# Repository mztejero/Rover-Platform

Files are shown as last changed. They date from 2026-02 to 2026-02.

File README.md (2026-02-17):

# Rover-Platform
ESP-IDF firmware, KiCad PCB, and Fusion360 Cad files  for a Rovere Platform

<p align="center">
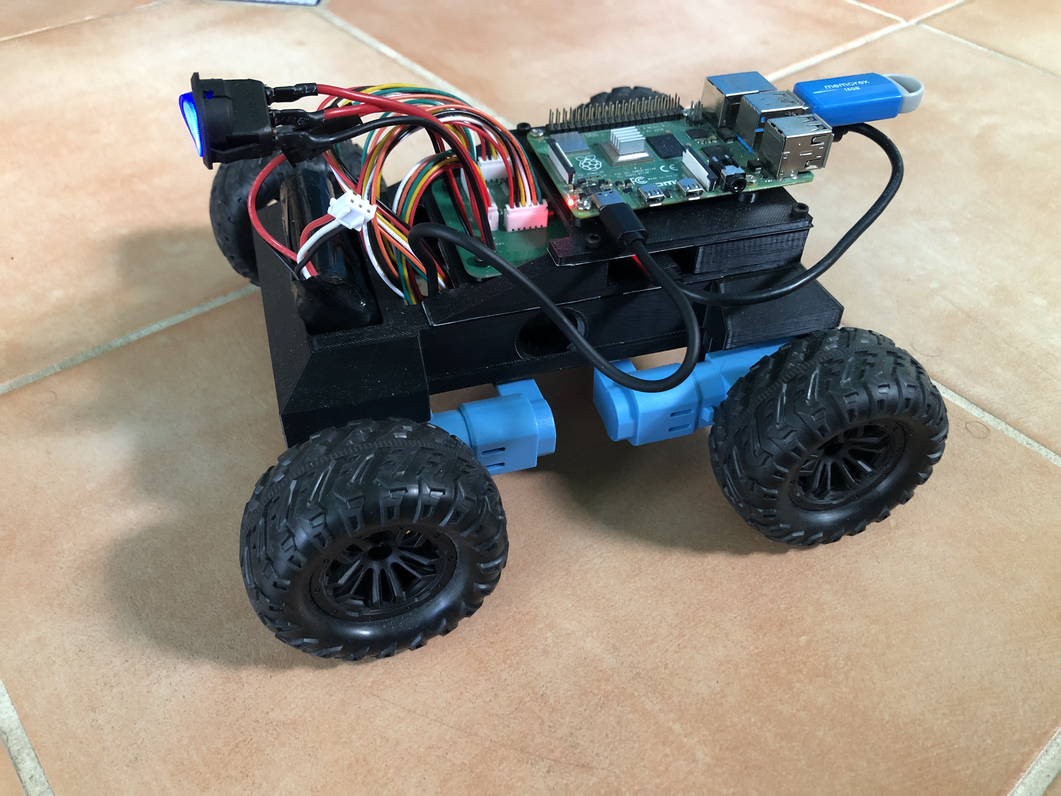
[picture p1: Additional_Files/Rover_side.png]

</p>

# ESP-IDF

The file architecture is split into each of the remote's functions with each .c file also havng a complementary .h file allowing variable and function sharng across the project. The files can be found in rover_firmware/main:

```
config.c
encoder.c
imu.c
motor.c
speed_controller.c
uart_interface.c
```

- ```config.c``` Sets up and names the GPIO's used on the ESP32.<br>
- ```encoder.c``` Reads interrupts on quadrature encoders A and B terminals and creates tasks for counting which are added to queues. This file also allows for reading wheel rotation and speed.<br>
- ```imu.c``` Communicates with onboard IMU via I<sup>2</sup>C in order to receive sensor readings from accelerometer and gyroscope.<br>
- ```motor.c``` Generates a PWM signal using timer and compare events and provides a function for controlling motor speed and direction through duty cycle.<br>
- ```speed_controller.c``` Controls motor speed using a PID and non linear gain to adjust duty cycle written to motor. The feedback is obtained from the encoders.<br>
- ```uart_interface.c``` Receives speed commands for all four motors and writes wheel rotation, speed, accelerometer, and gyroscope readings.<br>

  * The files with the extension "_module" were used for the breadboard module prototyping.
  *  There are files for communicating with onboard Magnetometer, however these are not currently being used.

# Schematics

<p align="center">
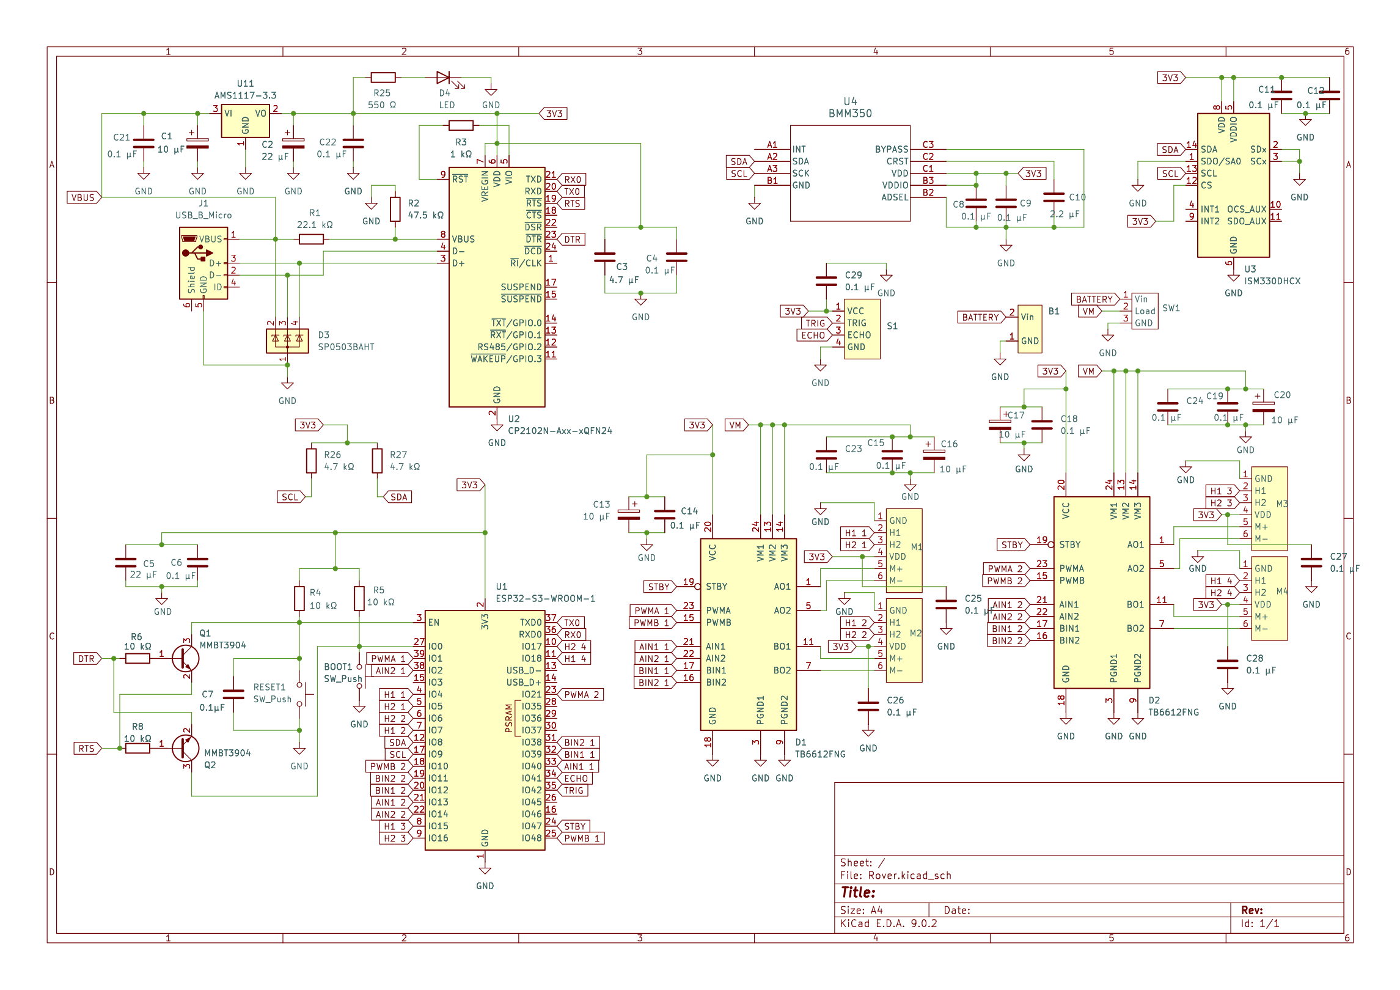
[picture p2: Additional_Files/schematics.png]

</p>

- ESP32-S3-WROOM-1: Microcontroller used to run firmware, read sensors, and write to actuators
- CP2102A USB-to-UART: Interface for UART reading and writing and for uploading code to the ESP32-WROOM-32E. The NPN transistors circuitry automatically put the ESP32 into bootloader mode when a new upload happens.
- TB6612FNG: Dual Motor driver used for interfacing with 2 DC Motors. Uses A and B pins for motor direction and a PWM pin.
- ISM330DHCX: IMU chip used for accelerometer and gyroscope feedback. Uses I<sup>2</sup>C protocol for communication.

Chips not currently used
  • BMM350: Magnetometer chip with I<sup>2</sup>C protocol for communication.

# Final PCB Design

<p align="center">
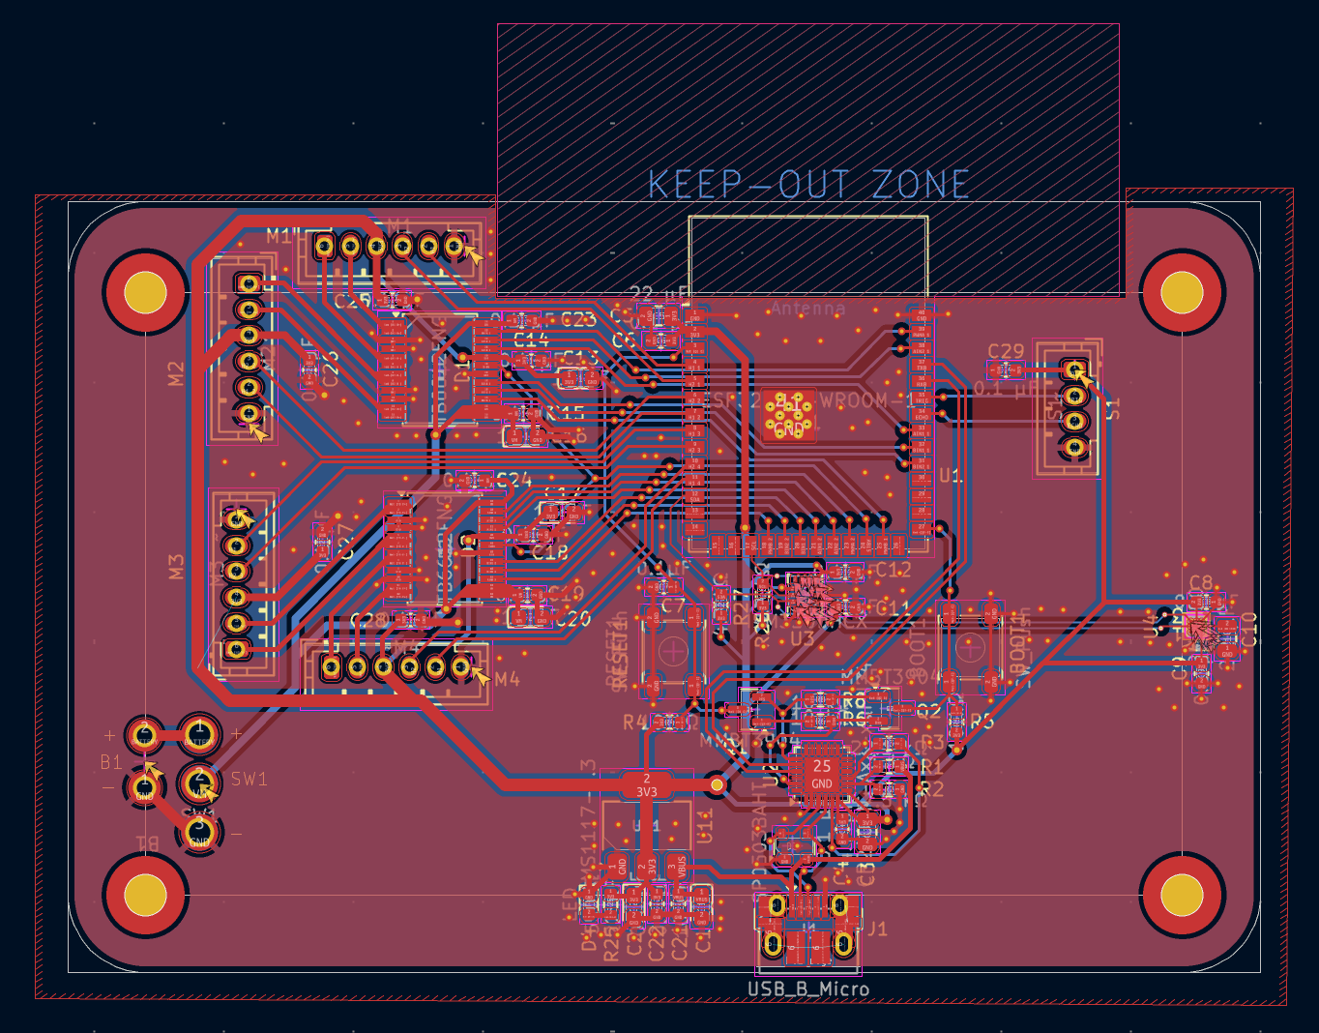
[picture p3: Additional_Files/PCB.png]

</p>
<p align="center">
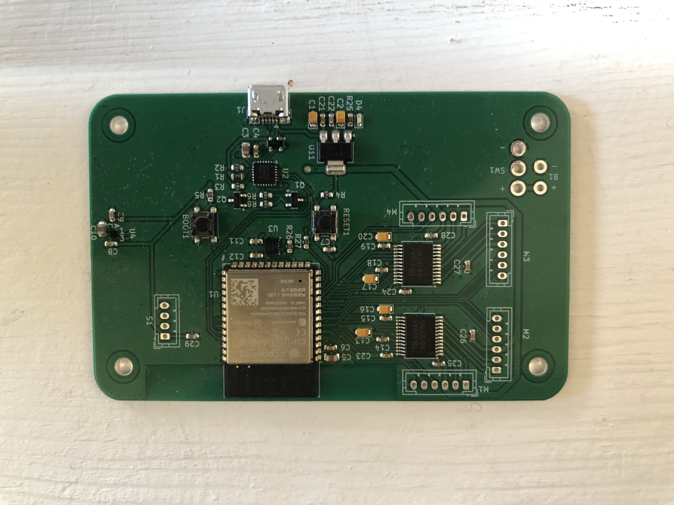
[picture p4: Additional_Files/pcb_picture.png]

</p>

# Final Rover CAD Design
<p align="center">
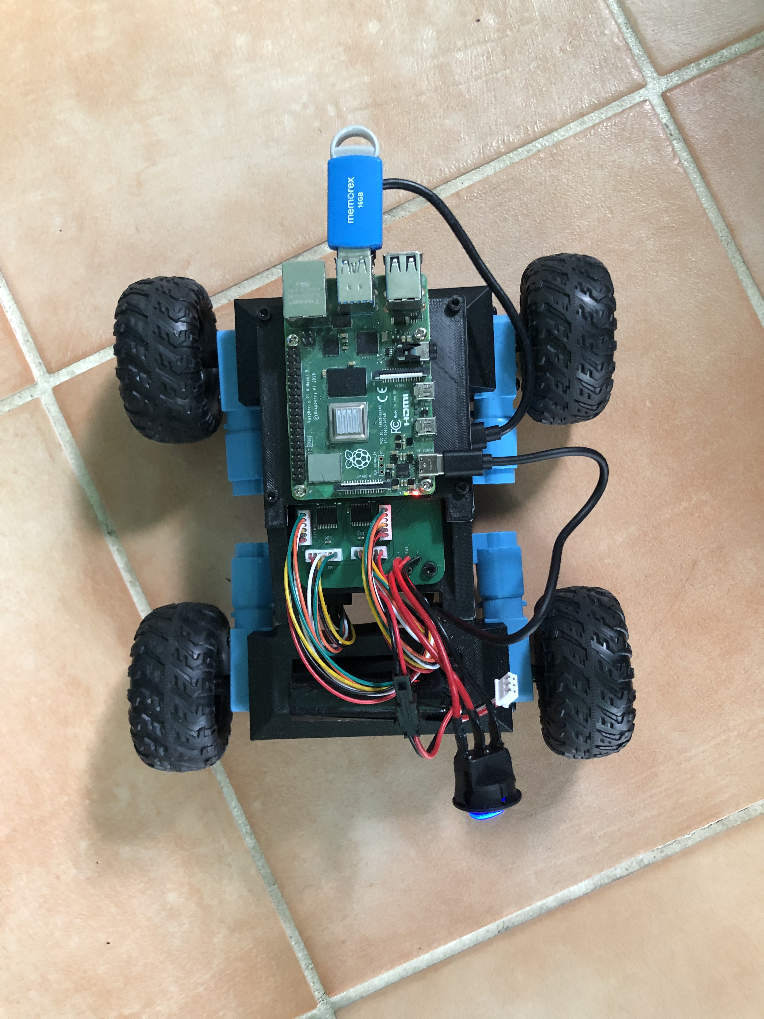
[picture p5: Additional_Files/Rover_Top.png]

</p>

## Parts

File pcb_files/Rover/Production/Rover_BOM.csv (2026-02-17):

Comment | Designator | LCSC | MFR.Part # | Footprint
SW_Push | BOOT1, RESET1 | C2689502 | PTS647SM38SMTR2LFS | Button_Switch_SMD:SW_SPST_PTS647_Sx38
10 uF | C1, C13, C16, C17, C20 | C313067 | TLJR106M010R2000 | Capacitor_Tantalum_SMD:CP_EIA-2012-12_Kemet-R
22 uF | C2 | C11383 | TAJR106M006RNJ | Capacitor_Tantalum_SMD:CP_EIA-2012-12_Kemet-R
4.7 uF | C3 | C1779 | CL21A475KAQNNNE | Capacitor_SMD:C_0805_2012Metric
0.1 uF | C4, C6, C7, C8, C9, C11, C12, C14, C15, C18, C19, C21, C22, C23, C24, C25, C26, C27, C28, C29 | C14663 | CC0603KRX7R9BB104 | Capacitor_SMD:C_0603_1608Metric
22 uF | C5 | C45783 | CL21A226MAQNNNE | Capacitor_SMD:C_0805_2012Metric
2.2 uF | C10 | C377773 | 0805X7R225K630NT | Capacitor_SMD:C_0805_2012Metric
TB6612FNG | D1, D2 | C141517 | TB6612FNG,C,8,EL | Package_SO:SSOP-24_5.3x8.2mm_P0.65mm
SP0503BAHT | D3 | C7074 | SP0503BAHTG | Package_TO_SOT_SMD:SOT-143
LED | D4 | C2286 | KT-0603R | LED_SMD:LED_0603_1608Metric
USB_B_Micro | J1 | C428495 | 10103594-0001LF | Connector_USB:USB_Micro-B_Amphenol_10103594-0001LF_Horizontal
MMBT3904 | Q1, Q2 | C20526 | MMBT3904 | Package_TO_SOT_SMD:SOT-23
22.1 k ohm | R1 | C325880 | RMC080522.1K1%N | Resistor_SMD:R_0603_1608Metric
47.5 k ohm | R2 | C23061 | 0603WAF4752T5E | Resistor_SMD:R_0603_1608Metric
1 k ohm | R3 | C21190 | 0603WAF1001T5E | Resistor_SMD:R_0603_1608Metric
10 k ohm | R4, R5, R6, R8 | C25804 | 0603WAF1002T5E | Resistor_SMD:R_0603_1608Metric
560 ohm | R25 | C23204 | 0603WAF5600T5E | Resistor_SMD:R_0603_1608Metric
4.7 k ohm | R26, R27 | C25999 | 0603WAJ0472T5E | Resistor_SMD:R_0603_1608Metric
ESP32-S3-WROOM-1 | U1 | C2913198 | ESP32-S3-WROOM-1-N8 | RF_Module:ESP32-S3-WROOM-1
CP2102N | U2 | C969151 | CP2102N-A02-GQFN24R | Package_DFN_QFN:QFN-24-1EP_4x4mm_P0.5mm_EP2.6x2.6mm
ISM330DHCX | U3 | C2655101 | ISM330DHCXTR | Package_LGA:LGA-14_3x2.5mm_P0.5mm_LayoutBorder3x4y
BMM350 | U4 | C17225907 | WLCSP-9(1.3x1.3) | footprints:BGA9_BMM350_BOS
AMS1117-3.3 | U11 | C6186 | AMS1117-3.3 | Package_TO_SOT_SMD:SOT-223-3_TabPin2

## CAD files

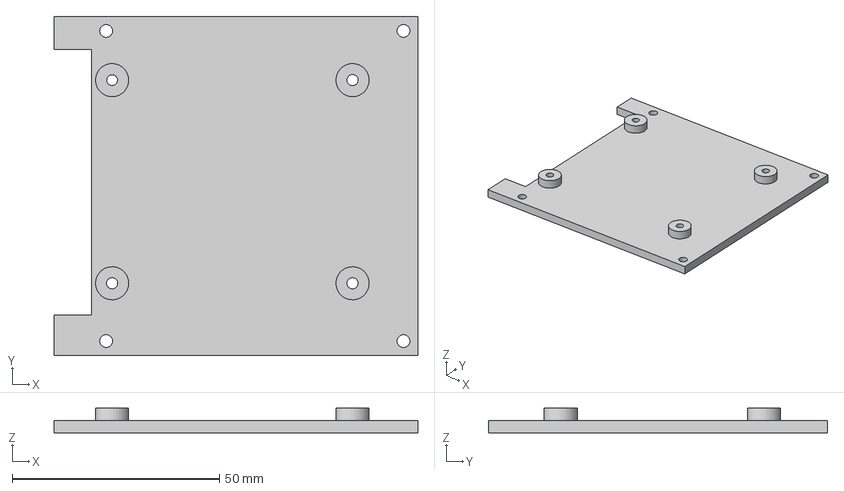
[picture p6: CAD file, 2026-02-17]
cad_files/Rover/RPI Stand.3mf
87.8 x 81.8 x 6.00 mm

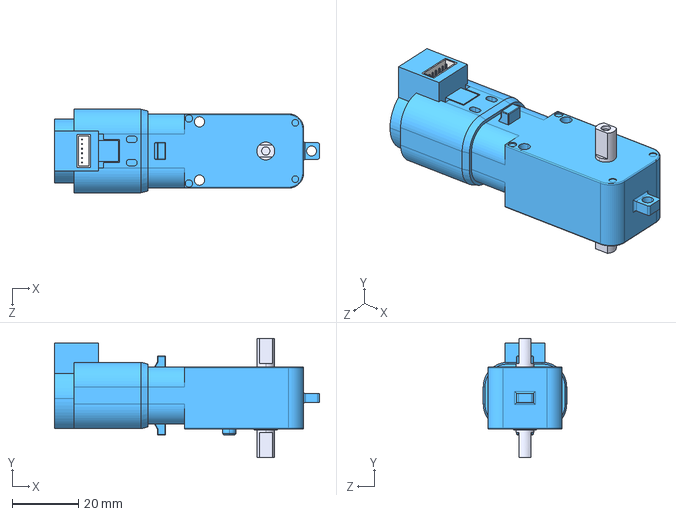
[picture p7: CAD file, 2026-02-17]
cad_files/Rover/motor.STEP
80.0 x 36.1 x 25.2 mm

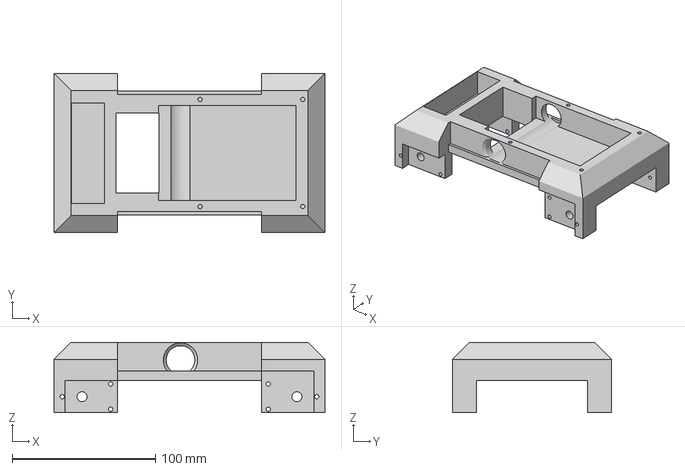
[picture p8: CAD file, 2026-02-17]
cad_files/Rover/Rover Body.3mf
189.2 x 111.2 x 49.2 mm

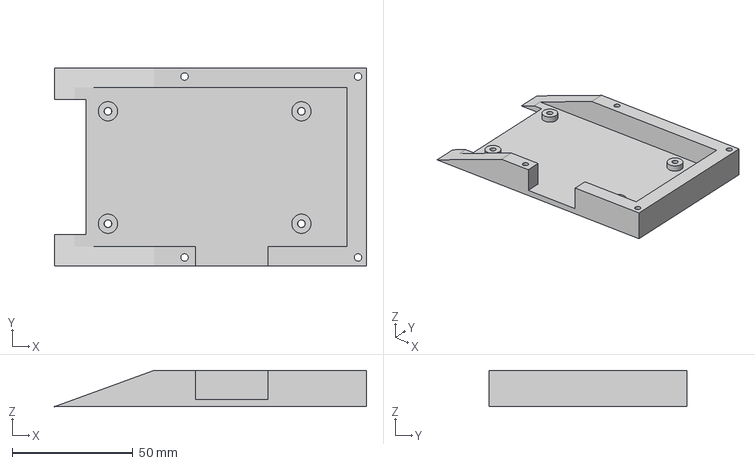
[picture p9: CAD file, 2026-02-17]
cad_files/Rover/PCB Stand.3mf
129.0 x 81.8 x 15.0 mm

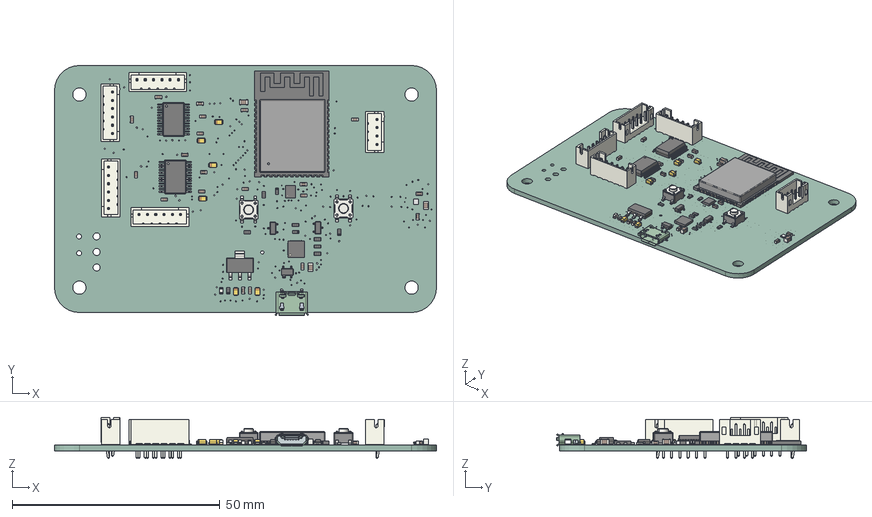
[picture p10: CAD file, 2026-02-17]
cad_files/Rover/Rover_pcb.step
92.0 x 60.2 x 9.90 mm
CP_EIA-2012-12_Kemet-R x 6
C_0603_1608Metric x 20
R_0603_1608Metric x 10
BMM350
LED_0603_1608Metric
SSOP-24_5.3x8.2mm_P0.65mm x 2
QFN-24-1EP_4x4mm_P0.5mm_EP2.6x2.6mm
JST_PH_B6B-PH-K_1x06_P2.00mm_Vertical x 4
ESP32-S3-WROOM-1
SW_SPST_PTS647Sx38 x 2
LGA-14_3x2.5mm_P0.5mm_LayoutBorder3x4y
C_0805_2012Metric x 3
SOT-23 x 2
SOT-223
SOT-143
JST_PH_B4B-PH-K_1x04_P2.00mm_Vertical
Rover_PCB

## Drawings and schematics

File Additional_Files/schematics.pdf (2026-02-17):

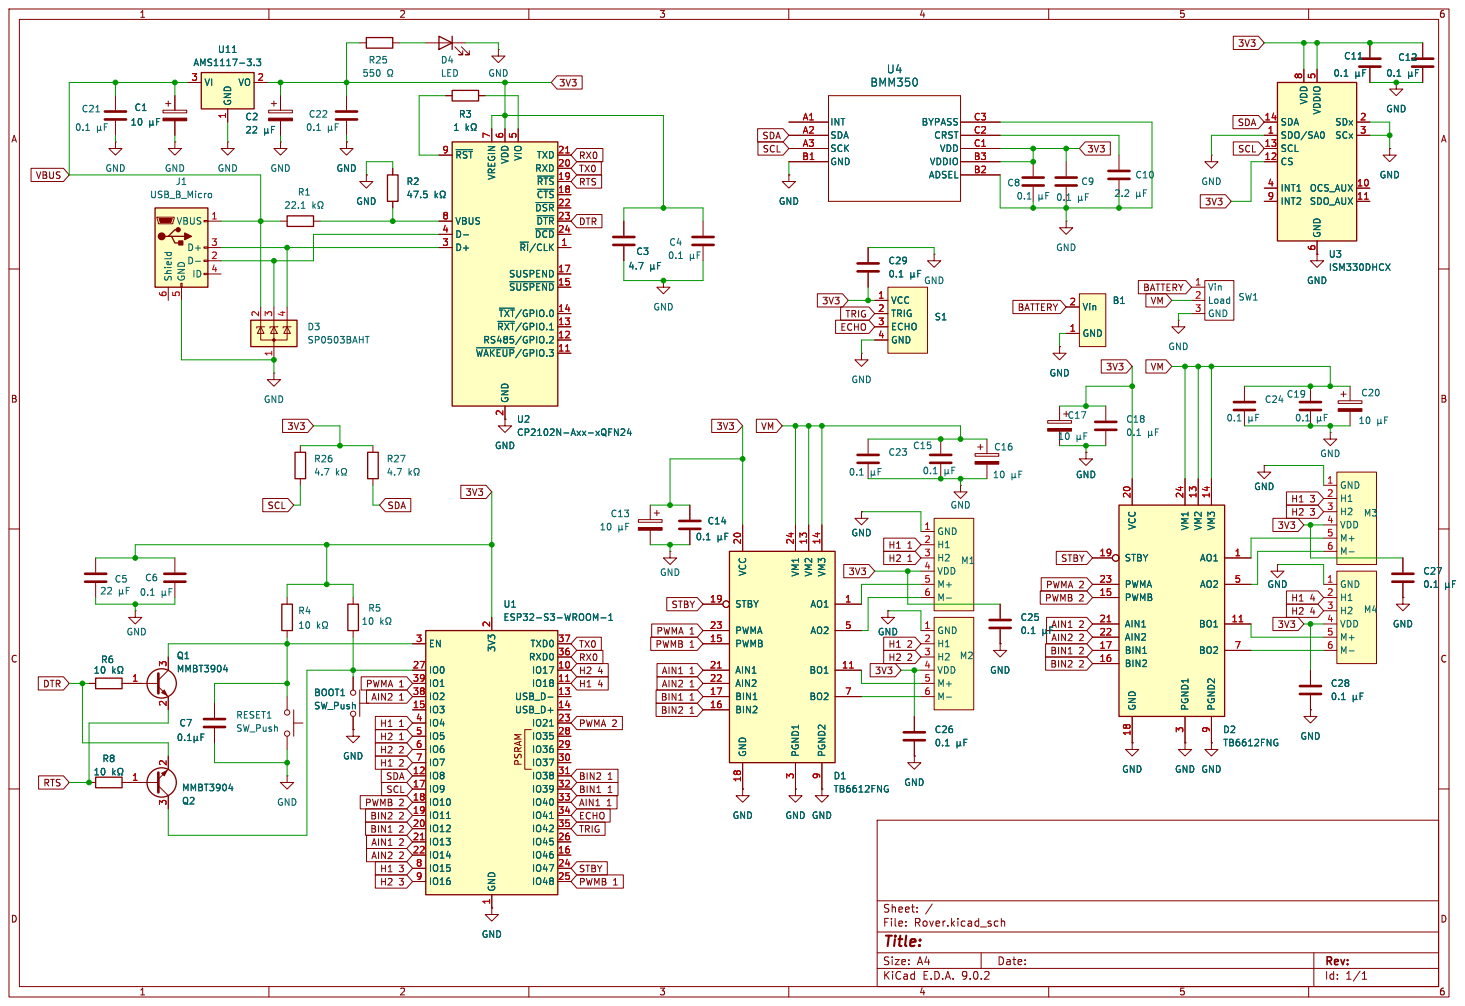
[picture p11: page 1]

SDA 14 SDO/SA0 1 SCL 13 CS 12
SDA

5 TXD 21 RXD 20 ~{RTS} 19 ~{CTS} 18 ~{DSR} 22 ~{DTR} 23 ~{DCD} 24 ~{RI}/CLK1 SUSPEND 17 ~{SUSPEND}15 ~{TXT}/GPIO.014 ~{RXT}/GPIO.113 RS485/GPIO.2 12 ~{WAKEUP}/GPIO.311 U2 CP2102N-Axx-xQFN24 C3

5 TXD 21 RXD 20 ~{RTS} 19 ~{CTS} 18 ~{DSR} 22 ~{DTR} 23 ~{DCD} 24 ~{RI}/CLK1 SUSPEND 17 ~{SUSPEND}15 ~{TXT}/GPIO.014 ~{RXT}/GPIO.113 RS485/GPIO.2 12 ~{WAKEUP}/GPIO.311 C3

0.1 þÿµF B1 Vin 2 GND 1 GND GND GND GND

Id: 1/1 Title: File: Rover.kicad_sch Sheet: / GND

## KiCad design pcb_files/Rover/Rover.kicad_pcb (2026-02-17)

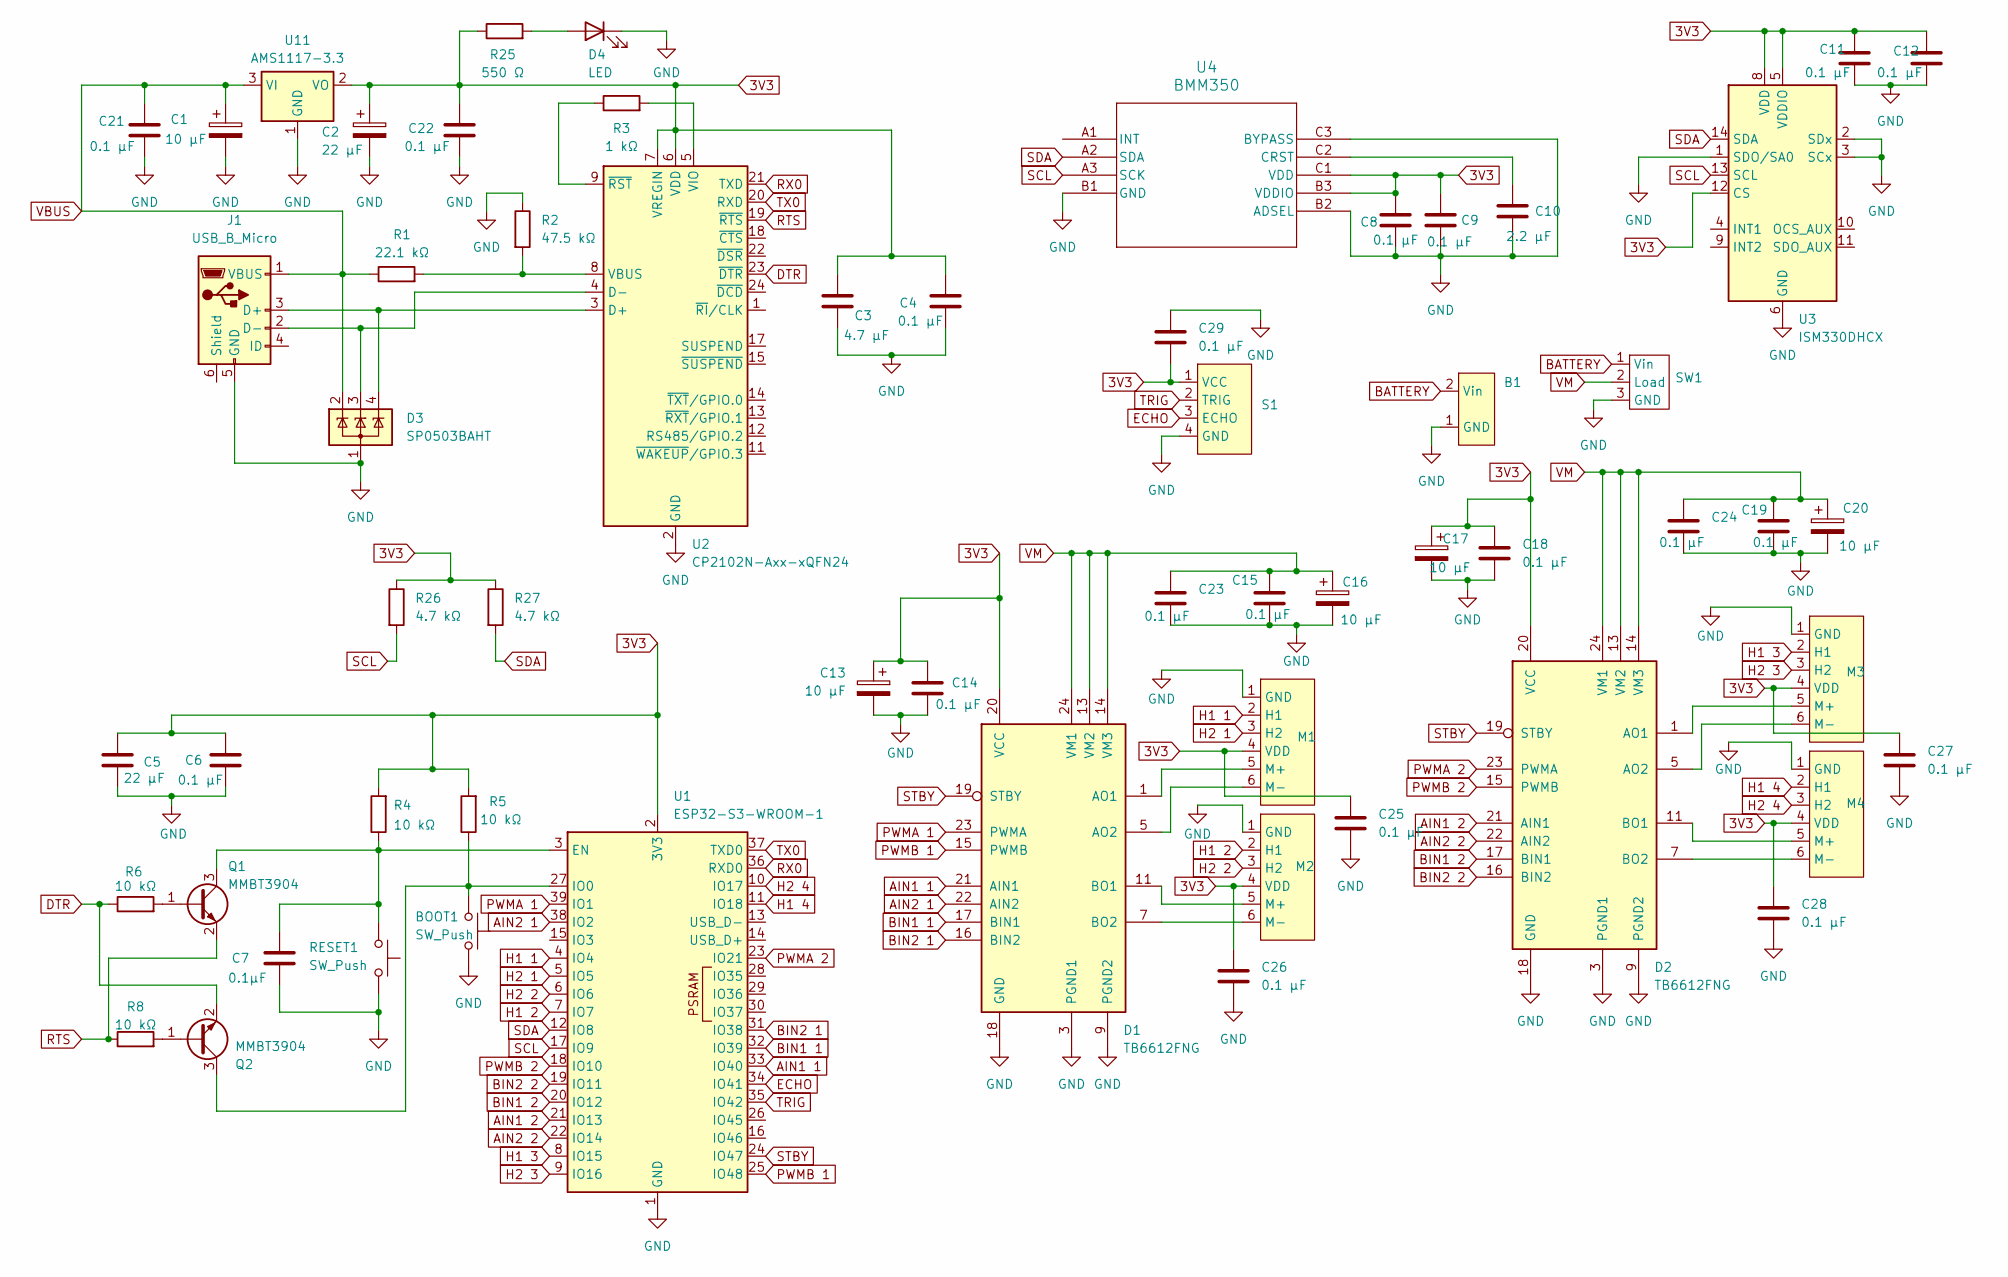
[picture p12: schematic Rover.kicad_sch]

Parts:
B1: Battery
BOOT1: SW_Push; SW_SPST_PTS647_Sx38
C1, C13, C16, C17, C20: 10 µF; CP_EIA-2012-12_Kemet-R
C2: 22 µF; CP_EIA-2012-12_Kemet-R
C3: 4.7 µF; C_0805_2012Metric
C4, C6, C8, C9, C11, C12, C14, C15, C18, C19, C21, C22, C23, C24, C25, C26, C27, C28, C29: 0.1 µF; C_0603_1608Metric
C5: 22 µF; C_0805_2012Metric
C7: 0.1µF; C_0603_1608Metric
C10: 2.2 µF; C_0805_2012Metric
D1, D2: TB6612FNG; SSOP-24_5.3x8.2mm_P0.65mm
D3: SP0503BAHT; SOT-143
D4: LED; LED_0603_1608Metric
J1: USB_B_Micro; USB_Micro-B_Amphenol_10103594-0001LF_Horizontal
M1, M2, M3, M4: JST_PH_B6B-PH-K_1x06_P2.00mm_Vertical
Q1, Q2: MMBT3904; SOT-23
R1: 22.1 kΩ; R_0603_1608Metric
R2: 47.5 kΩ; R_0603_1608Metric
R3: 1 kΩ; R_0603_1608Metric
R4, R5, R6, R8: 10 kΩ; R_0603_1608Metric
R25: 550 Ω; R_0603_1608Metric
R26, R27: 4.7 kΩ; R_0603_1608Metric
RESET1: SW_Push; SW_SPST_PTS647_Sx38
S1: JST_PH_B4B-PH-K_1x04_P2.00mm_Vertical
SW1: Switch
U1: ESP32-S3-WROOM-1
U2: CP2102N-Axx-xQFN24; QFN-24-1EP_4x4mm_P0.5mm_EP2.6x2.6mm
U3: ISM330DHCX; LGA-14_3x2.5mm_P0.5mm_LayoutBorder3x4y
U4: BMM350; BGA9_BMM350_BOS
U11: AMS1117-3.3; SOT-223-3_TabPin2

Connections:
3V3: C2.1, C3.1, C4.1, C5.1, C6.1, C8.2, C9.1, C11.1, C12.1, C13.1, C14.1, C17.1, C18.1, C22.1, C25.1, C26.1, C27.1, C28.1, C29.2, D1.20 (VCC), D2.20 (VCC), M1.4 (VDD), M2.4 (VDD), M3.4 (VDD), M4.4 (VDD), R4.2, R5.2, R25.1, R26.1, R27.1, S1.1 (VCC), U1.2 (3V3), U2.6 (VDD), U2.7 (VREGIN), U3.5 (VDDIO), U3.8 (VDD), U3.12 (CS), U4.B3 (VDDIO), U4.C1 (VDD), U11.2 (VO)
AIN1 1: D1.21 (AIN1), U1.33 (IO40)
AIN1 2: D2.21 (AIN1), U1.21 (IO13)
AIN2 1: D1.22 (AIN2), U1.38 (IO2)
AIN2 2: D2.22 (AIN2), U1.22 (IO14)
BATTERY: B1.2 (Vin), SW1.1 (Vin)
BIN1 1: D1.17 (BIN1), U1.32 (IO39)
BIN1 2: D2.17 (BIN1), U1.20 (IO12)
BIN2 1: D1.16 (BIN2), U1.31 (IO38)
BIN2 2: D2.16 (BIN2), U1.19 (IO11)
DTR: Q2.2 (E), R6.1, U2.23 (~DTR)
ECHO: S1.3 (ECHO), U1.34 (IO41)
GND: B1.1 (GND), BOOT1.2, C1.2, C2.2, C3.2, C4.2, C5.2, C6.2, C7.2, C8.1, C9.2, C10.1, C11.2, C12.2, C13.2, C14.2, C15.2, C16.2, C17.2, C18.2, C19.2, C20.2, C21.2, C22.2, C23.2, C24.2, C25.2, C26.2, C27.2, C28.2, C29.1, D1.3 (PGND1), D1.4 (PGND1), D1.9 (PGND2), D1.10 (PGND2), D1.18 (GND), D2.3 (PGND1), D2.4 (PGND1), D2.9 (PGND2), D2.10 (PGND2), D2.18 (GND), D3.1 (A), D4.1 (K), J1.5 (GND), M1.1 (GND), M2.1 (GND), M3.1 (GND), M4.1 (GND), R2.1, RESET1.2, S1.4 (GND), SW1.3 (GND), U1.1 (GND), U1.40 (GND), U1.41 (GND), U2.2 (GND), U2.25 (GND), U3.1 (SDO/SA0), U3.2 (SDx), U3.3 (SCx), U3.6 (GND), U3.7 (GND), U4.B1 (GND), U4.B2 (ADSEL), U4.C3 (BYPASS), U11.1 (GND)
H1 1: M1.2 (H1), U1.4 (IO4)
H1 2: M2.2 (H1), U1.7 (IO7)
H1 3: M3.2 (H1), U1.8 (IO15)
H1 4: M4.2 (H1), U1.11 (IO18)
H2 1: M1.3 (H2), U1.5 (IO5)
H2 2: M2.3 (H2), U1.6 (IO6)
H2 3: M3.3 (H2), U1.9 (IO16)
H2 4: M4.3 (H2), U1.10 (IO17)
unnamed: D4.2 (A), R25.2
unnamed: D3.4 (K), J1.3 (D+), U2.3 (D+)
unnamed: D3.3 (K), J1.2 (D-), U2.4 (D-)
unnamed: D1.1 (AO1), D1.2 (AO1), M1.5 (M+)
unnamed: D1.5 (AO2), D1.6 (AO2), M1.6 (M-)
unnamed: D1.11 (BO1), D1.12 (BO1), M2.5 (M+)
unnamed: D1.7 (BO2), D1.8 (BO2), M2.6 (M-)
unnamed: D2.1 (AO1), D2.2 (AO1), M3.5 (M+)
unnamed: D2.5 (AO2), D2.6 (AO2), M3.6 (M-)
unnamed: D2.11 (BO1), D2.12 (BO1), M4.5 (M+)
unnamed: D2.7 (BO2), D2.8 (BO2), M4.6 (M-)
unnamed: Q1.1 (B), R6.2
unnamed: C7.1, Q1.3 (C), R4.1, RESET1.1, U1.3 (EN)
unnamed: Q2.1 (B), R8.2
unnamed: BOOT1.1, Q2.3 (C), R5.1, U1.27 (IO0)
unnamed: R1.2, R2.2, U2.8 (VBUS)
unnamed: R3.2, U2.5 (VIO)
unnamed: R3.1, U2.9 (~RST)
unnamed: C10.2, U4.C2 (CRST)
PWMA 1: D1.23 (PWMA), U1.39 (IO1)
PWMA 2: D2.23 (PWMA), U1.23 (IO21)
PWMB 1: D1.15 (PWMB), U1.25 (IO48)
PWMB 2: D2.15 (PWMB), U1.18 (IO10)
RTS: Q1.2 (E), R8.1, U2.19 (~RTS)
RX0: U1.36 (RXD0), U2.21 (TXD)
SCL: R26.2, U1.17 (IO9), U3.13 (SCL), U4.A3 (SCK)
SDA: R27.2, U1.12 (IO8), U3.14 (SDA), U4.A2 (SDA)
STBY: D1.19 (STBY), D2.19 (STBY), U1.24 (IO47)
TRIG: S1.2 (TRIG), U1.35 (IO42)
TX0: U1.37 (TXD0), U2.20 (RXD)
VBUS: C1.1, C21.1, D3.2 (K), J1.1 (VBUS), R1.1, U11.3 (VI)
VM: C15.1, C16.1, C19.1, C20.1, C23.1, C24.1, D1.13 (VM2), D1.14 (VM3), D1.24 (VM1), D2.13 (VM2), D2.14 (VM3), D2.24 (VM1), SW1.2 (Load)

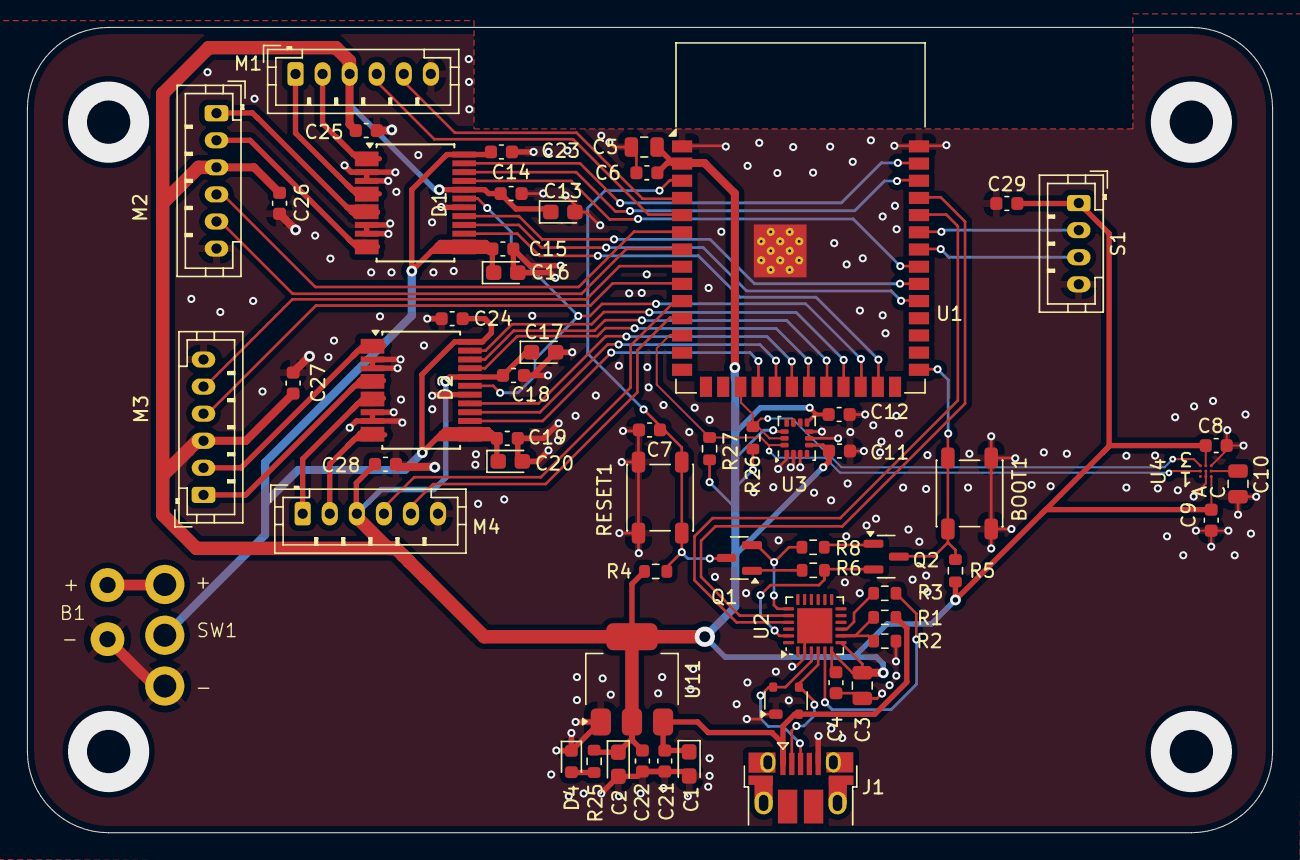
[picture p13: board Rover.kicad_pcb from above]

Board: 2 copper layers, 92.0 x 59.5 mm, 60 parts (0 on the bottom side), 53 nets.

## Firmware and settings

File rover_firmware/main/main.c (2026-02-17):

// idf.py -p /dev/cu.usbserial-0001 -b 115200 flash monitor
#include "config.h"
#include "imu.h"
#include "magnetometer.h"
#include "motor.h"
#include "encoder.h"
#include "speed_controller.h"
#include "uart_interface.h"

void app_main (void) {
    setup_gpio();

    vTaskDelay(pdMS_TO_TICKS(50));

    setup_i2c();
    setup_imu_i2c();
    // setup_mag_i2c();
    setup_uart();

    xTaskCreatePinnedToCore(imu_task, "imu_task", 8192, NULL, 4, NULL, 0);
    // xTaskCreatePinnedToCore(mag_task, "mag_task", 8192, NULL, 4, NULL, 0);
    xTaskCreate(uart_read_task, "uart_task", 8192, NULL, 4, NULL);
    xTaskCreate(uart_write_task, "uart_task", 8192, NULL, 4, NULL);

    enc_table();
    setup_queues();
    setup_isr();
    create_enc_timer();

    setup_motors();

    while(1) {
        set_motor_speed(v1_ref, v2_ref, v3_ref, v4_ref);
        vTaskDelay(pdMS_TO_TICKS(10));
        get_count();
    }
}

// idf.py -p /dev/cu.usbmodem14101 -b 115200 flash monitor
// idf.py -p /dev/cu.usbmodem14101 -b 115200 monitor

// idf.py -p /dev/cu.usbserial-0001 -b 115200 flash monitor
// idf.py -p /dev/cu.usbserial-0001 -b 115200 monitor

// CUSTOM PCB

// idf.py -p /dev/cu.usbserial-1410 -b 115200 flash monitor
// idf.py -p /dev/cu.usbserial-1410 -b 115200 monitor

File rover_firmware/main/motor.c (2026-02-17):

#include "config.h"

#include <stdbool.h>
#include <stdio.h>
#include "driver/gpio.h"
#include "freertos/FreeRTOS.h"
#include "driver/mcpwm_timer.h"
#include "driver/mcpwm_oper.h"
#include "driver/mcpwm_cmpr.h"
#include "driver/mcpwm_gen.h"
// #include "driver/mcpwm_prelude.h" 

#define PWM_FREQ 80e6
#define PWM_TICKS 8000

// Handles
static mcpwm_timer_handle_t pwm_12_timer_handle = NULL;
static mcpwm_timer_handle_t pwm_34_timer_handle = NULL;


static mcpwm_oper_handle_t pwm_12_oper_handle = NULL;
static mcpwm_oper_handle_t pwm_34_oper_handle = NULL;

static mcpwm_cmpr_handle_t pwm_1_cmpr_handle = NULL;
static mcpwm_cmpr_handle_t pwm_2_cmpr_handle = NULL;
static mcpwm_cmpr_handle_t pwm_3_cmpr_handle = NULL;
static mcpwm_cmpr_handle_t pwm_4_cmpr_handle = NULL;

static mcpwm_gen_handle_t pwm_1_gen_handle = NULL;
static mcpwm_gen_handle_t pwm_2_gen_handle = NULL;
static mcpwm_gen_handle_t pwm_3_gen_handle = NULL;
static mcpwm_gen_handle_t pwm_4_gen_handle = NULL;

void setup_motors(void) {
    // TIMER
    mcpwm_timer_config_t pwm_12_timer_config = {
        .group_id = 0,
        .intr_priority = 0,
        .clk_src = MCPWM_TIMER_CLK_SRC_PLL160M,
        .resolution_hz = PWM_FREQ,
        .count_mode = MCPWM_TIMER_COUNT_MODE_UP,
        .period_ticks = PWM_TICKS
    };
    mcpwm_timer_config_t pwm_34_timer_config = {
        .group_id = 1,
        .intr_priority = 0,
        .clk_src = MCPWM_TIMER_CLK_SRC_PLL160M,
        .resolution_hz = PWM_FREQ,
        .count_mode = MCPWM_TIMER_COUNT_MODE_UP,
        .period_ticks = PWM_TICKS
    };
    ESP_ERROR_CHECK(mcpwm_new_timer(&pwm_12_timer_config, &pwm_12_timer_handle));
    ESP_ERROR_CHECK(mcpwm_new_timer(&pwm_34_timer_config, &pwm_34_timer_handle));

    // OPERATOR
    mcpwm_operator_config_t pwm_12_operator_config = {
        .group_id = 0,
        .intr_priority = 0
    };
    mcpwm_operator_config_t pwm_34_operator_config = {
        .group_id = 1,
        .intr_priority = 0
    };

    ESP_ERROR_CHECK(mcpwm_new_operator(&pwm_12_operator_config, &pwm_12_oper_handle));
    ESP_ERROR_CHECK(mcpwm_new_operator(&pwm_34_operator_config, &pwm_34_oper_handle));
    ESP_ERROR_CHECK(mcpwm_operator_connect_timer(pwm_12_oper_handle, pwm_12_timer_handle));
    ESP_ERROR_CHECK(mcpwm_operator_connect_timer(pwm_34_oper_handle, pwm_34_timer_handle));

    // COMPARATOR
    mcpwm_comparator_config_t pwm_1_comparator_config = {
        .intr_priority = 0
    };
    mcpwm_comparator_config_t pwm_2_comparator_config = {
        .intr_priority = 0
    };
    mcpwm_comparator_config_t pwm_3_comparator_config = {
        .intr_priority = 0
    };
    mcpwm_comparator_config_t pwm_4_comparator_config = {
        .intr_priority = 0
    };
    
    ESP_ERROR_CHECK(mcpwm_new_comparator(pwm_12_oper_handle, &pwm_1_comparator_config, &pwm_1_cmpr_handle));
    ESP_ERROR_CHECK(mcpwm_new_comparator(pwm_12_oper_handle, &pwm_2_comparator_config, &pwm_2_cmpr_handle));
    ESP_ERROR_CHECK(mcpwm_new_comparator(pwm_34_oper_handle, &pwm_3_comparator_config, &pwm_3_cmpr_handle));
    ESP_ERROR_CHECK(mcpwm_new_comparator(pwm_34_oper_handle, &pwm_4_comparator_config, &pwm_4_cmpr_handle));

    // GENERATOR
    mcpwm_generator_config_t pwm_1_generator_config = {
        .gen_gpio_num = pins.pwm_1
    };
    mcpwm_generator_config_t pwm_2_generator_config = {
        .gen_gpio_num = pins.pwm_2
    };
    mcpwm_generator_config_t pwm_3_generator_config = {
        .gen_gpio_num = pins.pwm_3
    };
    mcpwm_generator_config_t pwm_4_generator_config = {
        .gen_gpio_num = pins.pwm_4
    };
    ESP_ERROR_CHECK(mcpwm_new_generator(pwm_12_oper_handle, &pwm_1_generator_config, &pwm_1_gen_handle));
    ESP_ERROR_CHECK(mcpwm_new_generator(pwm_12_oper_handle, &pwm_2_generator_config, &pwm_2_gen_handle));
    ESP_ERROR_CHECK(mcpwm_new_generator(pwm_34_oper_handle, &pwm_3_generator_config, &pwm_3_gen_handle));
    ESP_ERROR_CHECK(mcpwm_new_generator(pwm_34_oper_handle, &pwm_4_generator_config, &pwm_4_gen_handle));

    // EVENTS
    // Timer event
    mcpwm_gen_timer_event_action_t pwm_12_timer_event = {
        .direction = MCPWM_TIMER_DIRECTION_UP,
        .event = MCPWM_TIMER_EVENT_EMPTY,
        .action = MCPWM_GEN_ACTION_HIGH
    };
    mcpwm_gen_timer_event_action_t pwm_34_timer_event = {
        .direction = MCPWM_TIMER_DIRECTION_UP,
        .event = MCPWM_TIMER_EVENT_EMPTY,
        .action = MCPWM_GEN_ACTION_HIGH
    };

    // Compare events
    mcpwm_gen_compare_event_action_t pwm_1_compare_event = {
        .direction = MCPWM_TIMER_DIRECTION_UP,
        .comparator = pwm_1_cmpr_handle,
        .action = MCPWM_GEN_ACTION_LOW
    };
    mcpwm_gen_compare_event_action_t pwm_2_compare_event = {
        .direction = MCPWM_TIMER_DIRECTION_UP,
        .comparator = pwm_2_cmpr_handle,
        .action = MCPWM_GEN_ACTION_LOW
    };
    mcpwm_gen_compare_event_action_t pwm_3_compare_event = {
        .direction = MCPWM_TIMER_DIRECTION_UP,
        .comparator = pwm_3_cmpr_handle,
        .action = MCPWM_GEN_ACTION_LOW
    };
    mcpwm_gen_compare_event_action_t pwm_4_compare_event = {
        .direction = MCPWM_TIMER_DIRECTION_UP,
        .comparator = pwm_4_cmpr_handle,
        .action = MCPWM_GEN_ACTION_LOW
    };

    ESP_ERROR_CHECK(mcpwm_generator_set_action_on_timer_event(pwm_1_gen_handle, pwm_12_timer_event));
    ESP_ERROR_CHECK(mcpwm_generator_set_action_on_timer_event(pwm_2_gen_handle, pwm_12_timer_event));
    ESP_ERROR_CHECK(mcpwm_generator_set_action_on_timer_event(pwm_3_gen_handle, pwm_34_timer_event));
    ESP_ERROR_CHECK(mcpwm_generator_set_action_on_timer_event(pwm_4_gen_handle, pwm_34_timer_event));

    ESP_ERROR_CHECK(mcpwm_generator_set_action_on_compare_event(pwm_1_gen_handle, pwm_1_compare_event));
    ESP_ERROR_CHECK(mcpwm_generator_set_action_on_compare_event(pwm_2_gen_handle, pwm_2_compare_event));
    ESP_ERROR_CHECK(mcpwm_generator_set_action_on_compare_event(pwm_3_gen_handle, pwm_3_compare_event));
    ESP_ERROR_CHECK(mcpwm_generator_set_action_on_compare_event(pwm_4_gen_handle, pwm_4_compare_event));

    // Start Timer
    ESP_ERROR_CHECK(mcpwm_timer_enable(pwm_12_timer_handle));
    ESP_ERROR_CHECK(mcpwm_timer_enable(pwm_34_timer_handle));
    ESP_ERROR_CHECK(mcpwm_timer_start_stop(pwm_12_timer_handle, MCPWM_TIMER_START_NO_STOP));
    ESP_ERROR_CHECK(mcpwm_timer_start_stop(pwm_34_timer_handle, MCPWM_TIMER_START_NO_STOP));
    // ESP_LOGI("MOTOR", "Timer started. Ticks = %d", PWM_TICKS);
}
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

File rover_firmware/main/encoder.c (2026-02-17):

#include "config.h"

#include <stdio.h>
#include "freertos/FreeRTOS.h"
#include "freertos/task.h"
#include "driver/gptimer.h"
#include "driver/gptimer_types.h"

#define TIMER_FREQ 1000000 // Hz
#define RESOLUTION 576 // PPR
#define PI 3.14159
#define WHEEL_RADIUS 7e-2 // m

// Global Variables
volatile int count_1;
volatile int count_2;
volatile int count_3;
volatile int count_4;

// Define Handles
QueueHandle_t queue_1;
QueueHandle_t queue_2;
QueueHandle_t queue_3;
QueueHandle_t queue_4;

// Encoder Lookup Table
int8_t enc[256] = {0};
void enc_table(void) {
    enc[0b0001] = -1;
    enc[0b0111] = -1;
    enc[0b1110] = -1;
    enc[0b1000] = -1;

    enc[0b0010] = 1;
    enc[0b0100] = 1;
    enc[0b1101] = 1;
    enc[0b1011] = 1;
}

// ISR's
void IRAM_ATTR enc_1_isr_handler(void *arg) {
    static uint8_t state_1 = 0b1111;

    uint8_t enc1 = gpio_get_level(pins.enc1_1);
    uint8_t enc2 = gpio_get_level(pins.enc2_1);

    uint8_t curr = (enc1 << 1) | enc2;
    state_1 = (state_1 << 2) | curr;
    uint8_t state = state_1;

    BaseType_t xHPW = pdFALSE;
    xQueueSendFromISR(queue_1, &state, &xHPW);
    if (xHPW) portYIELD_FROM_ISR();
}

void IRAM_ATTR enc_2_isr_handler(void *arg) {
    static uint8_t state_2 = 0b1111;

    uint8_t enc1 = gpio_get_level(pins.enc1_2);
    uint8_t enc2 = gpio_get_level(pins.enc2_2);
    
    uint8_t curr = (enc1 << 1) | enc2;
    state_2 = (state_2 << 2) | curr;
    uint8_t state = state_2;

    BaseType_t xHPW = pdFALSE;
    xQueueSendFromISR(queue_2, &state, &xHPW);
    if (xHPW) portYIELD_FROM_ISR(); 
}

void IRAM_ATTR enc_3_isr_handler(void *arg) {
    static uint8_t state_3 = 0b1111;

    uint8_t enc1 = gpio_get_level(pins.enc1_3);
    uint8_t enc2 = gpio_get_level(pins.enc2_3);
    
    uint8_t curr = (enc1 << 1) | enc2;
    state_3 = (state_3 << 2) | curr;
    uint8_t state = state_3;

    BaseType_t xHPW = pdFALSE;
    xQueueSendFromISR(queue_3, &state, &xHPW);
    if (xHPW) portYIELD_FROM_ISR(); 
}

void IRAM_ATTR enc_4_isr_handler(void *arg) {
    static uint8_t state_4 = 0b1111;

    uint8_t enc1 = gpio_get_level(pins.enc1_4);
    uint8_t enc2 = gpio_get_level(pins.enc2_4);
    
    uint8_t curr = (enc1 << 1) | enc2;
    state_4 = (state_4 << 2) | curr;
    uint8_t state = state_4;

    BaseType_t xHPW = pdFALSE;
    xQueueSendFromISR(queue_4, &state, &xHPW);
    if (xHPW) portYIELD_FROM_ISR(); 
}

// void state_reader(uint8_t state) {
//     char binary_string[9];
//     for (int i = 7; i >= 0; --i) {
//         if ((state >> i) & 1) {
//             binary_string[7 - i] = '1';
//         }
//         else {
//             binary_string[7 - i] = '0';
//         }
//     }
//     binary_string[8] = '\0';
//     printf("binary: 0b%s\n", binary_string);
// }

void enc_1_isr_task(void *arg) {
    uint8_t state;
    while (1) {
        if (xQueueReceive(queue_1, &state, portMAX_DELAY) == pdTRUE) {
            count_1 += enc[state & 0x0F];
            // printf("count 1: %d\n", count_1);
        }
    }
}

void enc_2_isr_task(void *arg) {
    uint8_t state;
    while (1) {
        if (xQueueReceive(queue_2, &state, portMAX_DELAY) == pdTRUE) {
            count_2 += enc[state & 0x0F];
        }
    }
}

void enc_3_isr_task(void *arg) {
    uint8_t state;
    while (1) {
        if (xQueueReceive(queue_3, &state, portMAX_DELAY) == pdTRUE) {
            count_3 += enc[state & 0x0F];
        }
    }
}

void enc_4_isr_task(void *arg) {
    uint8_t state;
    while (1) {
        if (xQueueReceive(queue_4, &state, portMAX_DELAY) == pdTRUE) {
            count_4 += enc[state & 0x0F];
        }
    }
}

// Queue Setup
void setup_queues(void) {
    queue_1 = xQueueCreate(128, sizeof(uint8_t));
    queue_2 = xQueueCreate(128, sizeof(uint8_t));
    queue_3 = xQueueCreate(128, sizeof(uint8_t));
    queue_4 = xQueueCreate(128, sizeof(uint8_t));
    if (!queue_1 || !queue_2 || !queue_3 || !queue_4) {
        printf("Failed to create queues\n");
    }

    if (xTaskCreatePinnedToCore(enc_1_isr_task, "enc_1_isr_task", 4096, NULL, 2, NULL, 1) != pdPASS) {
        printf("Failed to create enc_1_isr_task\n");
    }
    if (xTaskCreatePinnedToCore(enc_2_isr_task, "enc_2_isr_task", 4096, NULL, 2, NULL, 1) != pdPASS) {
        printf("Failed to create enc_2_isr_task\n");
    }
    if (xTaskCreatePinnedToCore(enc_3_isr_task, "enc_3_isr_task", 4096, NULL, 2, NULL, 1) != pdPASS) {
        printf("Failed to create enc_3_isr_task\n");
    }
    if (xTaskCreatePinnedToCore(enc_4_isr_task, "enc_4_isr_task", 4096, NULL, 2, NULL, 1) != pdPASS) {
        printf("Failed to create enc_4_isr_task\n");
    }
}

// Timer
gptimer_handle_t gptimer;

gptimer_config_t timer_config = {
    .clk_src = GPTIMER_CLK_SRC_APB,
    .direction = GPTIMER_COUNT_UP,
    .resolution_hz = TIMER_FREQ,
};

gptimer_alarm_config_t alarm_config = {
    .alarm_count = 100000, // ticks to count to
    .reload_count = 0, // reset tick value
    .flags.auto_reload_on_alarm = true, // reset timer
};

uint64_t count;
int count_1_prev;
int count_2_prev;
int count_3_prev;
int count_4_prev;

double time;

double ds1;
double ds2;
double ds3;
double ds4;

double v1;
double v2;
double v3;
double v4;

static bool reset_count(gptimer_handle_t timer, const gptimer_alarm_event_data_t *edata, void *user_ctx) {
    // function to call on alarm
    time = (double)count / TIMER_FREQ;

    ds1 = (count_1 - count_1_prev) * 2 * PI * WHEEL_RADIUS / RESOLUTION;
    ds2 = (count_2 - count_2_prev) * 2 * PI * WHEEL_RADIUS / RESOLUTION;
    ds3 = (count_3 - count_3_prev) * 2 * PI * WHEEL_RADIUS / RESOLUTION;
    ds4 = (count_4 - count_4_prev) * 2 * PI * WHEEL_RADIUS / RESOLUTION;

    v1 = ds1 / time;
    v2 = ds2 / time;
    v3 = ds3 / time;
    v4 = ds4 / time;

    count_1_prev = count_1;
    count_2_prev = count_2;
    count_3_prev = count_3;
    count_4_prev = count_4;


    return false;
}

gptimer_event_callbacks_t gptimer_callback = {
    .on_alarm = reset_count, // Call the user callback function when the alarm event occurs
};

void create_enc_timer(void) {
    ESP_ERROR_CHECK(gptimer_new_timer(&timer_config, &gptimer));
    ESP_ERROR_CHECK(gptimer_set_alarm_action(gptimer, &alarm_config));
    ESP_ERROR_CHECK(gptimer_register_event_callbacks(gptimer, &gptimer_callback, NULL));
    ESP_ERROR_CHECK(gptimer_enable(gptimer));
    ESP_ERROR_CHECK(gptimer_start(gptimer));
}

void get_count(void) {
    ESP_ERROR_CHECK(gptimer_get_raw_count(gptimer, &count));
    // printf("COUNT: %d\n", count_1);
    // printf("v1: %f m/s, v2: %f m/s, v3: %f m/s, v4: %f m/s\n", v1, v2, v3, v4);
    // printf("count 1: %d, count 2: %d, count 3: %d, count 4: %d\n", count_1, count_2, count_3, count_4);
}
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
